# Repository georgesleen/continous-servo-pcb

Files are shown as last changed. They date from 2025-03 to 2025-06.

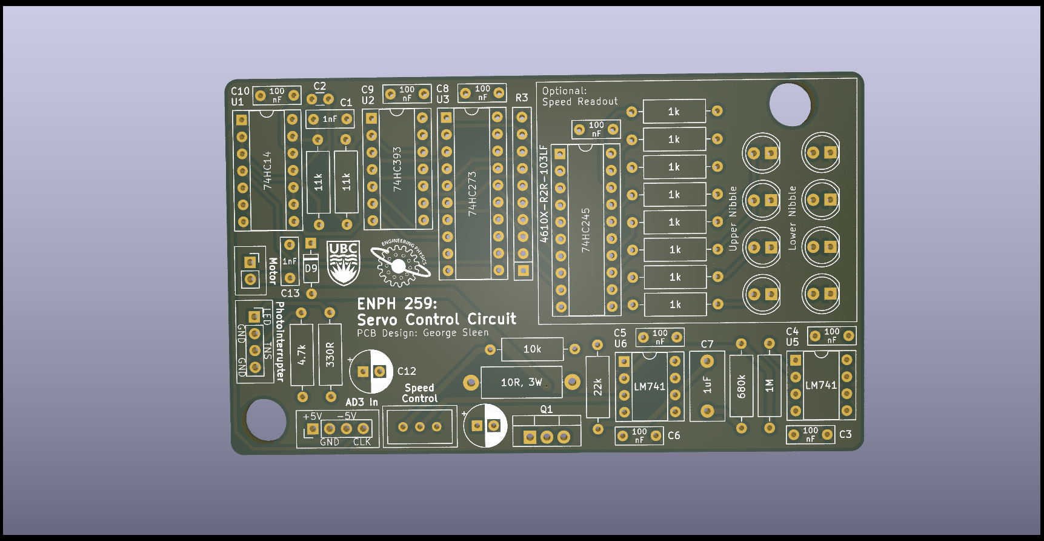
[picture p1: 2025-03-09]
images/enph259-servo-board-only.png

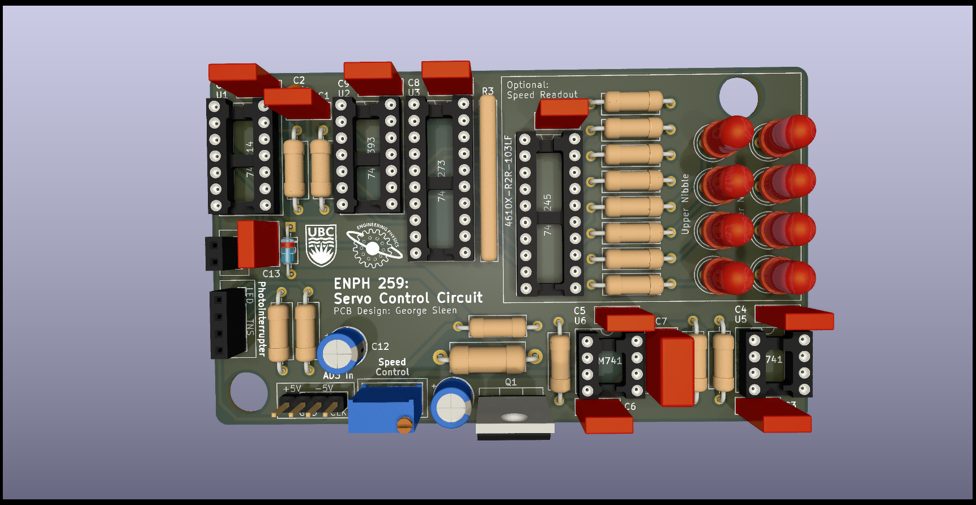
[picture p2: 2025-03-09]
images/enph259-servo.png

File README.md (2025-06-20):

# Continous rotation servo PCB.

Based on the final project from ENPH259. I've extended the project by creating a PCB and mechanical mount for the project.

I've also included an optional 'speed readout' on the board itself. This displays the current revolutions per cycle of the servo in binary.

By using slots in a disk attached to the motor shaft, I can monitor the rotational speed of the motor. This can then be fed into a counter that resets periodically, and is latched right before every reset. This digital number is then put through an R2R DAC, which is then compared with a reference voltage and fed into a PI controller, that runs a MOSFET driving the motor.

The project requires an external 5V, GND, -5V, and 5 Hz clock signal.

final-product
enph259-servo
enph259-servo-board-only

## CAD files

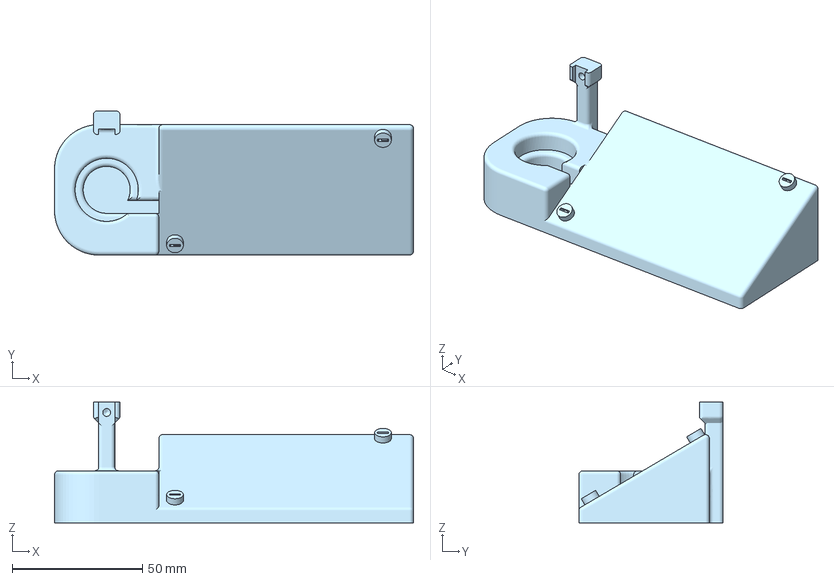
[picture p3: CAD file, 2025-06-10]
mount/enph259-pcb-mount.3mf
137.6 x 55.2 x 46.4 mm

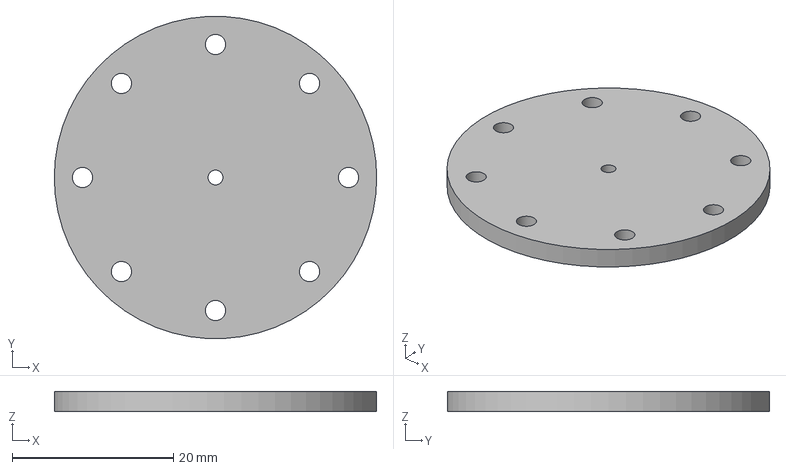
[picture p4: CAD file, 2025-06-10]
mount/enph259-photointerrupter-disk.3mf
40.0 x 39.9 x 2.50 mm

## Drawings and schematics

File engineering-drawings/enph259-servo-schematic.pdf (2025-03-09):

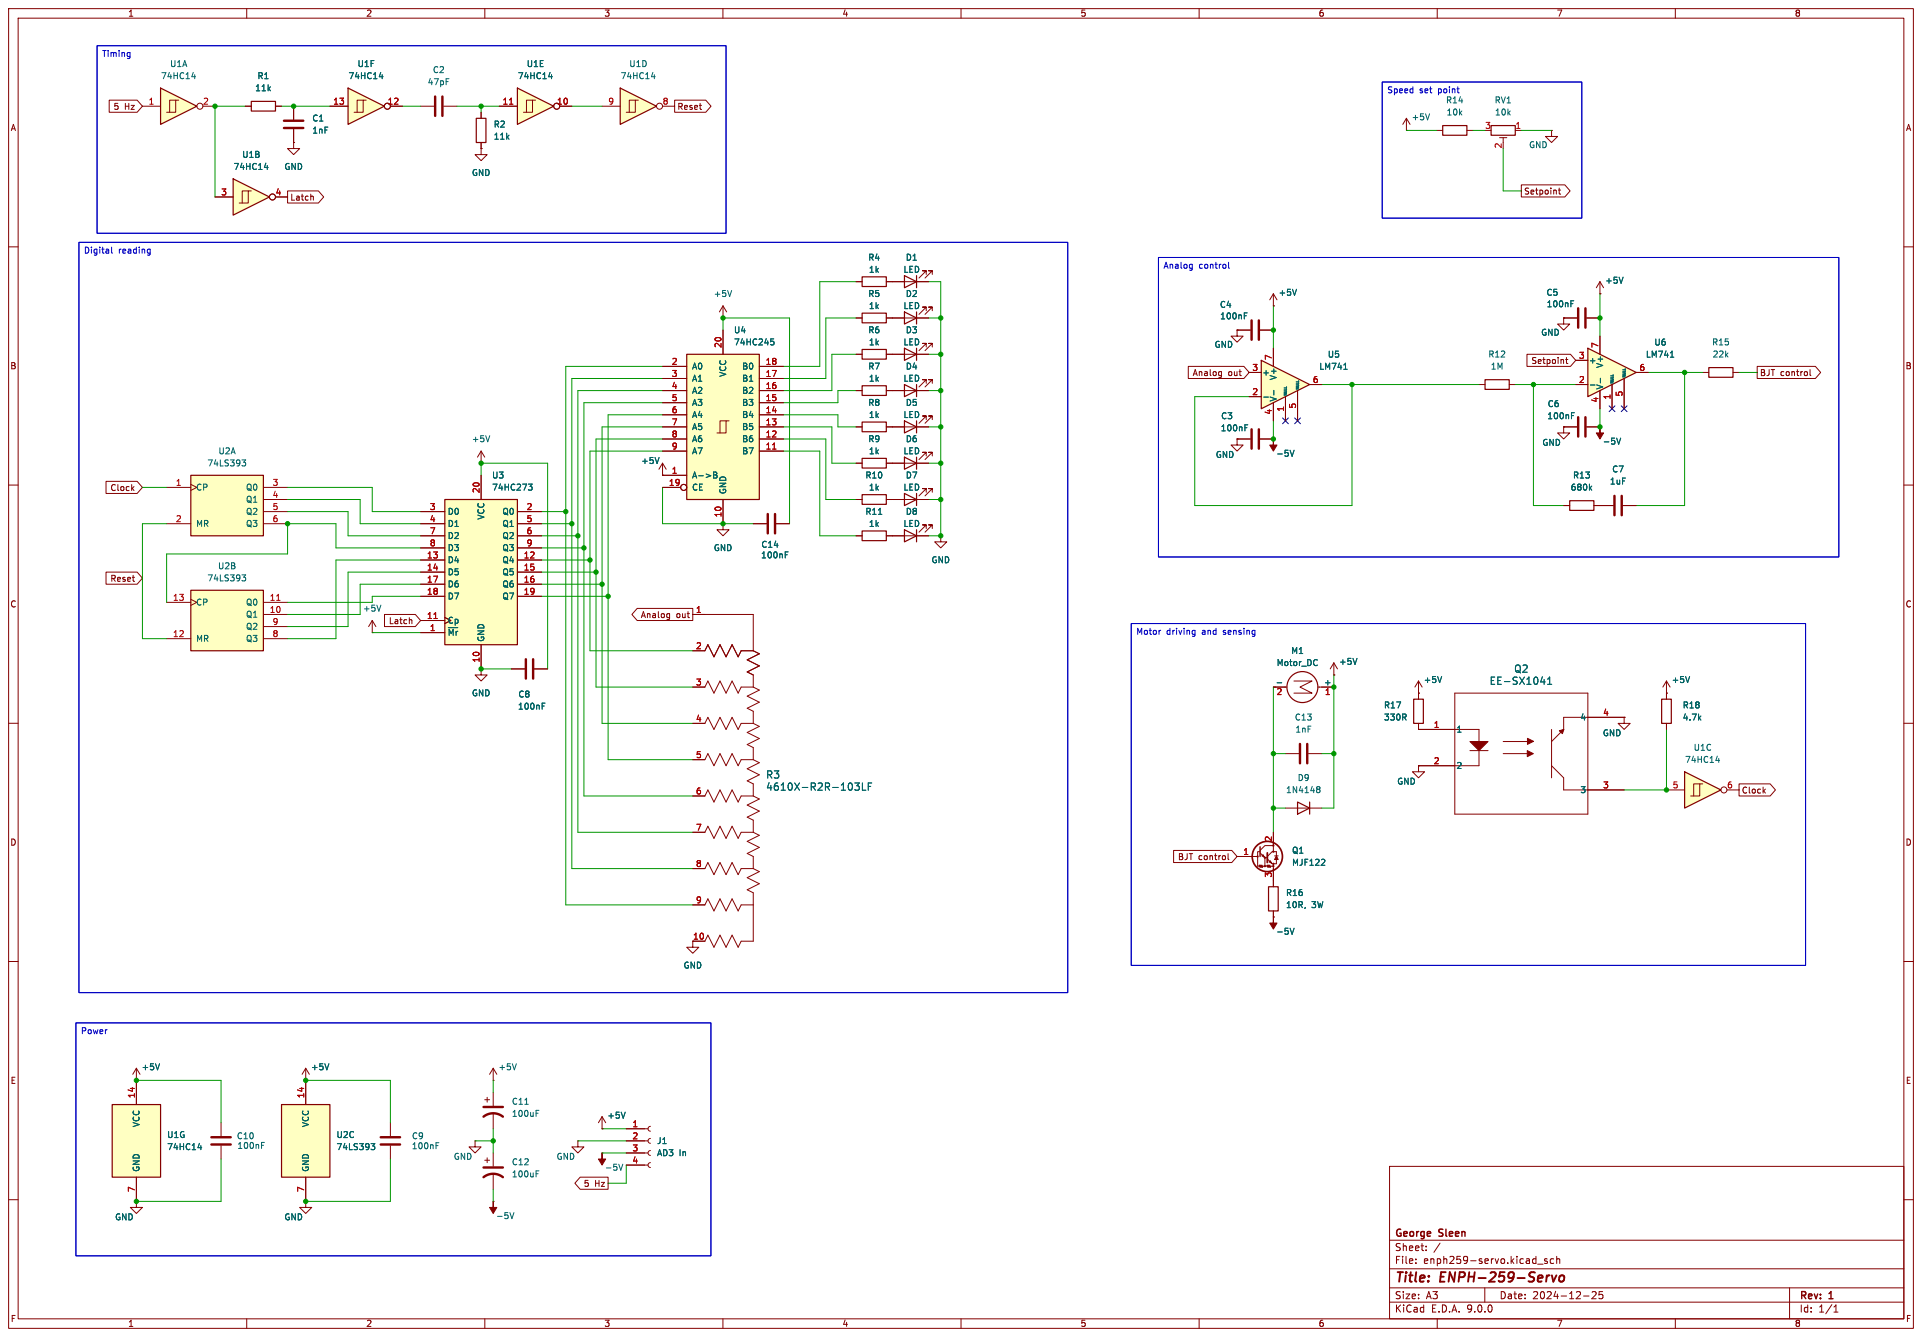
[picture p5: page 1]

Speed set point D7
Analog control Motor driving and sensing

File: enph259-servo.kicad_sch Sheet: / George Sleen

Id: 1/1 Title: ENPH-259-Servo

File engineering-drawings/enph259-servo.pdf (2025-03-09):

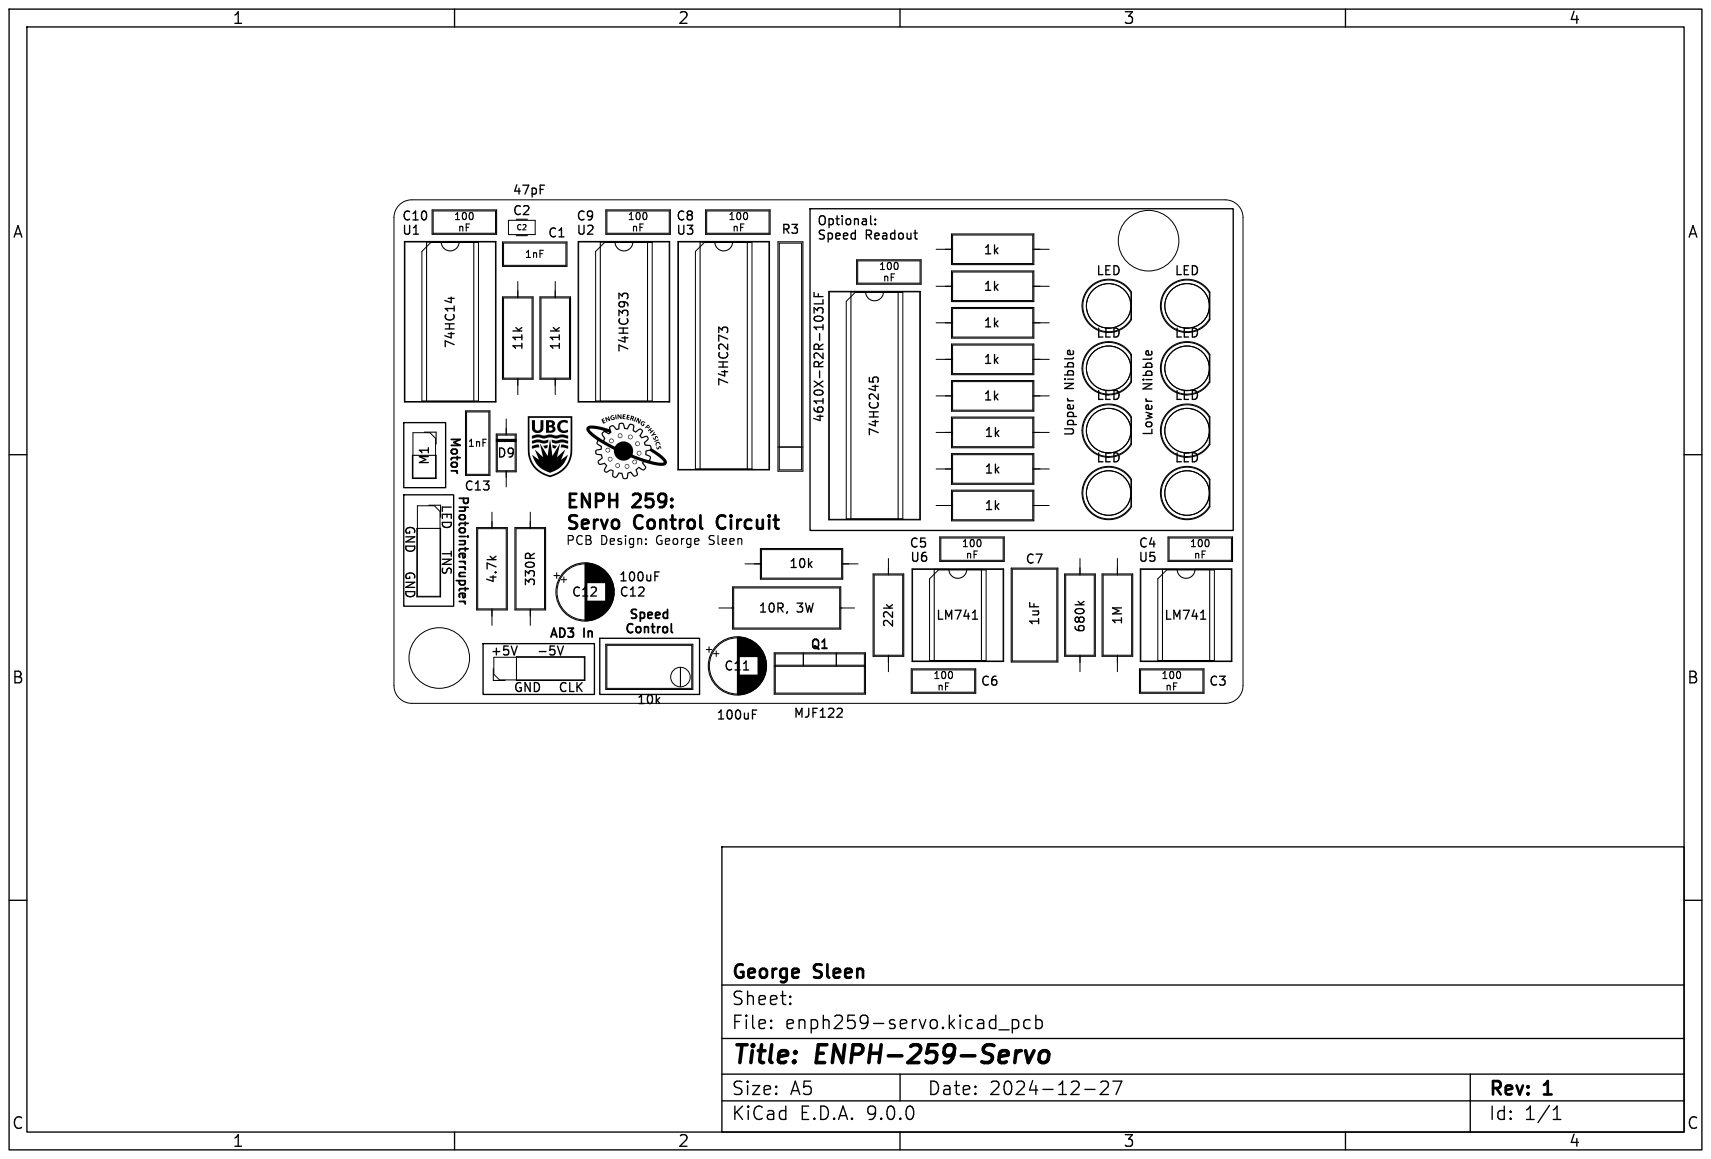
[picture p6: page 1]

File: enph259-servo.kicad_pcb Sheet: George Sleen 74HC245 Speed Control TNS Motor GND

Id: 1/1 Title: ENPH-259-Servo

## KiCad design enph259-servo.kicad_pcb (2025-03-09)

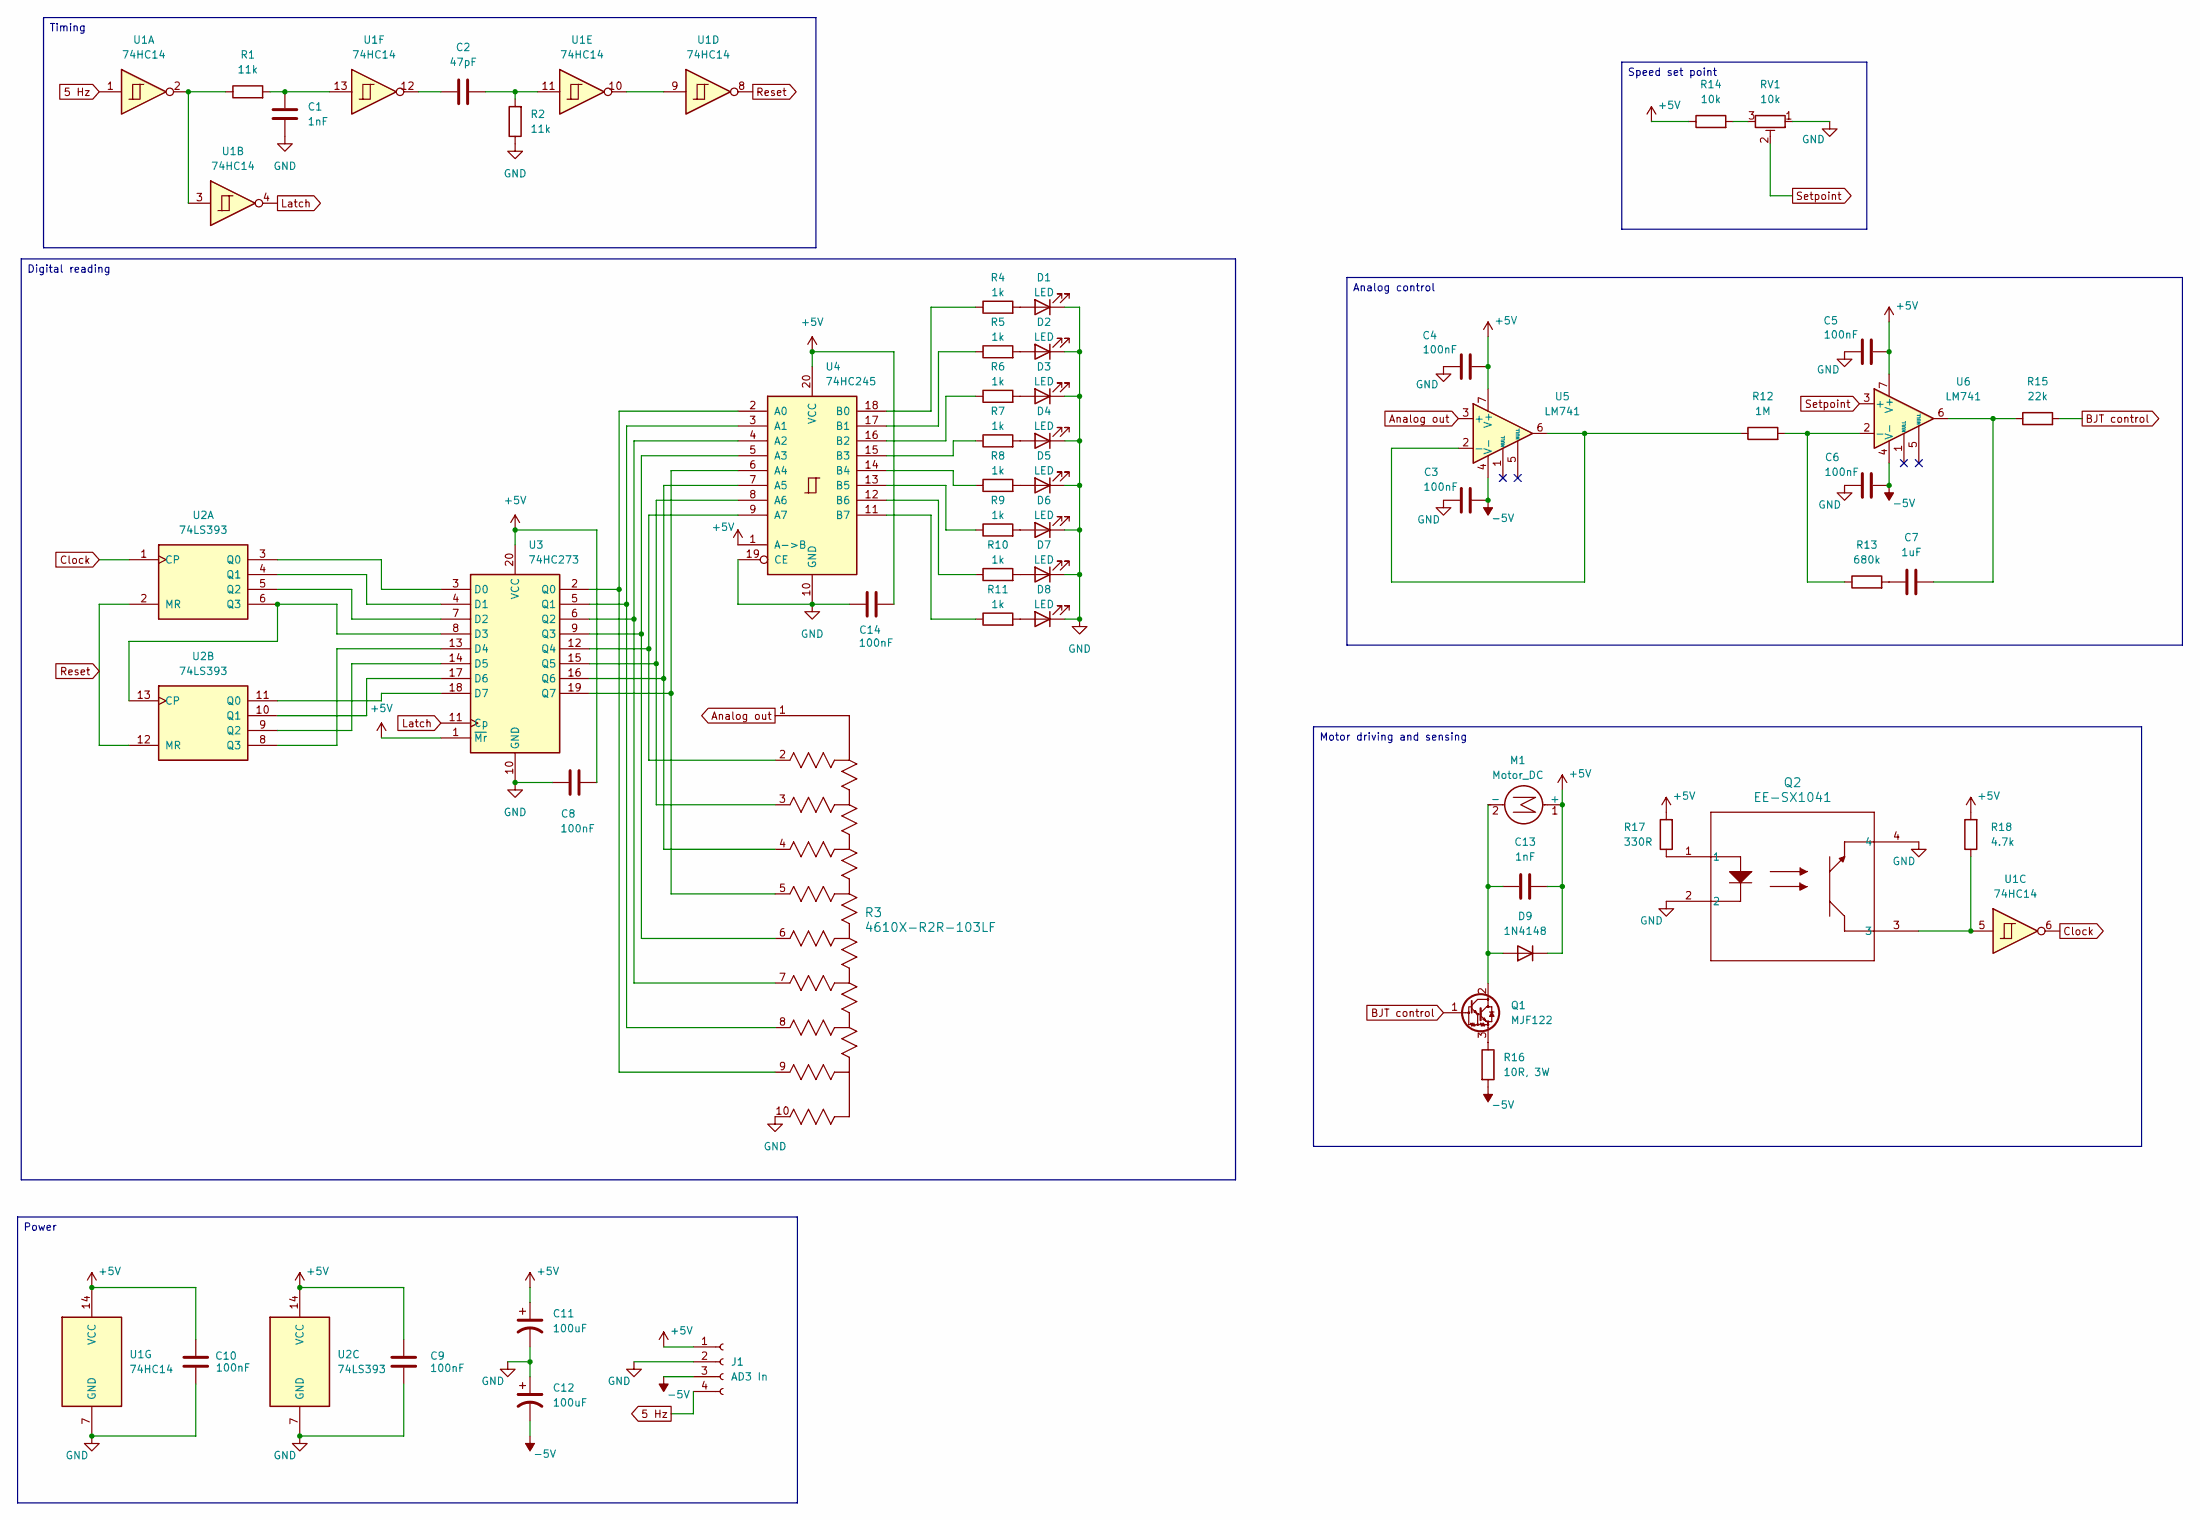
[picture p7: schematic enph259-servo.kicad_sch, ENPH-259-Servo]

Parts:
C1, C13: 1nF; C_Rect_L7.0mm_W2.5mm_P5.00mm
C2: 47pF; C_Disc_D3.0mm_W1.6mm_P2.50mm
C3, C4, C5, C6, C8, C9, C10, C14: 100nF; C_Rect_L7.0mm_W2.5mm_P5.00mm
C7: 1uF; C_Rect_L10.3mm_W5.0mm_P7.50mm_MKS4
C11, C12: 100uF; CP_Radial_D6.3mm_P2.50mm
D1, D2, D3, D4, D5, D6, D7, D8: LED; LED_D5.0mm
D9: 1N4148; D_DO-35_SOD27_P7.62mm_Horizontal
J1: AD3 In; PinHeader_1x04_P2.54mm_Vertical
M1: Motor_DC; PinSocket_1x02_P2.54mm_Vertical
Q1: MJF122; TO-220-3_Vertical
Q2: EE-SX1041; PinSocket_1x04_P2.54mm_Vertical
R1, R2: 11k; R_Axial_DIN0309_L9.0mm_D3.2mm_P12.70mm_Horizontal
R3: 4610X-R2R-103LF; R_Array_SIP10
R4, R5, R6, R7, R8, R9, R10, R11: 1k; R_Axial_DIN0309_L9.0mm_D3.2mm_P12.70mm_Horizontal
R12: 1M; R_Axial_DIN0309_L9.0mm_D3.2mm_P12.70mm_Horizontal
R13: 680k; R_Axial_DIN0309_L9.0mm_D3.2mm_P12.70mm_Horizontal
R14: 10k; R_Axial_DIN0309_L9.0mm_D3.2mm_P12.70mm_Horizontal
R15: 22k; R_Axial_DIN0309_L9.0mm_D3.2mm_P12.70mm_Horizontal
R16: 10R, 3W; R_Axial_DIN0414_L11.9mm_D4.5mm_P15.24mm_Horizontal
R17: 330R; R_Axial_DIN0309_L9.0mm_D3.2mm_P12.70mm_Horizontal
R18: 4.7k; R_Axial_DIN0309_L9.0mm_D3.2mm_P12.70mm_Horizontal
RV1: 10k; Potentiometer_Bourns_3296W_Vertical
U1: 74HC14; DIP-14_W7.62mm_Socket
U2: 74LS393; DIP-14_W7.62mm_Socket
U3: 74HC273; DIP-20_W7.62mm_Socket
U4: 74HC245; DIP-20_W7.62mm_Socket
U5, U6: LM741; DIP-8_W7.62mm_Socket

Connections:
5 Hz: J1.4, U1.1
+5V: C4.1, C5.1, C8.1, C9.1, C10.1, C11.1, C13.2, C14.2, D9.1 (K), J1.1, M1.1 (+), R14.1, R17.2, R18.2, U1.14 (VCC), U2.14 (VCC), U3.1 (~Mr), U3.20 (VCC), U4.1 (A->B), U4.20 (VCC), U5.7 (V+), U6.7 (V+)
-5V: C3.1, C6.1, C12.2, J1.3, R16.2, U5.4 (V-), U6.4 (V-)
Analog out: R3.1, U5.3 (+)
BJT control: Q1.1 (B), R15.2
Clock: U1.6, U2.1 (CP)
GND: C1.2, C3.2, C4.2, C5.2, C6.2, C8.2, C9.2, C10.2, C11.2, C12.1, C14.1, D1.1 (K), D2.1 (K), D3.1 (K), D4.1 (K), D5.1 (K), D6.1 (K), D7.1 (K), D8.1 (K), J1.2, Q2.2, Q2.4, R2.1, R3.10, RV1.1, U1.7 (GND), U2.7 (GND), U3.10 (GND), U4.10 (GND), U4.19 (CE)
Latch: U1.4, U3.11 (Cp)
unnamed: C1.1, R1.2, U1.13
unnamed: C2.1, U1.12
unnamed: C2.2, R2.2, U1.11
unnamed: C7.1, R13.2
unnamed: C7.2, R15.1, U6.6
unnamed: D1.2 (A), R4.2
unnamed: D2.2 (A), R5.2
unnamed: D3.2 (A), R6.2
unnamed: D4.2 (A), R7.2
unnamed: D5.2 (A), R8.2
unnamed: D6.2 (A), R9.2
unnamed: D7.2 (A), R10.2
unnamed: D8.2 (A), R11.2
unnamed: C13.1, D9.2 (A), M1.2 (-), Q1.2 (C)
unnamed: Q1.3 (E), R16.1
unnamed: Q2.1, R17.1
unnamed: Q2.3, R18.1, U1.5
unnamed: R1.1, U1.2, U1.3
unnamed: R14.2, RV1.3
unnamed: U1.9, U1.10
unnamed: U2.3 (Q0), U3.3 (D0)
unnamed: U2.4 (Q1), U3.4 (D1)
unnamed: U2.5 (Q2), U3.7 (D2)
unnamed: U2.6 (Q3), U2.13 (CP), U3.8 (D3)
unnamed: U2.11 (Q0), U3.18 (D7)
unnamed: U2.10 (Q1), U3.17 (D6)
unnamed: U2.9 (Q2), U3.14 (D5)
unnamed: U2.8 (Q3), U3.13 (D4)
unnamed: R3.9, U3.2 (Q0), U4.2 (A0)
unnamed: R3.8, U3.5 (Q1), U4.3 (A1)
unnamed: R3.7, U3.6 (Q2), U4.4 (A2)
unnamed: R3.6, U3.9 (Q3), U4.5 (A3)
unnamed: R3.2, U3.12 (Q4), U4.9 (A7)
unnamed: R3.3, U3.15 (Q5), U4.8 (A6)
unnamed: R3.4, U3.16 (Q6), U4.7 (A5)
unnamed: R3.5, U3.19 (Q7), U4.6 (A4)
unnamed: R4.1, U4.18 (B0)
unnamed: R5.1, U4.17 (B1)
unnamed: R6.1, U4.16 (B2)
unnamed: R7.1, U4.15 (B3)
unnamed: R8.1, U4.14 (B4)
unnamed: R9.1, U4.13 (B5)
unnamed: R10.1, U4.12 (B6)
unnamed: R11.1, U4.11 (B7)
unnamed: R12.1, U5.2 (-), U5.6
unnamed: R12.2, R13.1, U6.2 (-)
Reset: U1.8, U2.2 (MR), U2.12 (MR)
Setpoint: RV1.2, U6.3 (+)

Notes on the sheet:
Digital reading
Motor driving and sensing
Power
Speed set point
Analog control
Timing

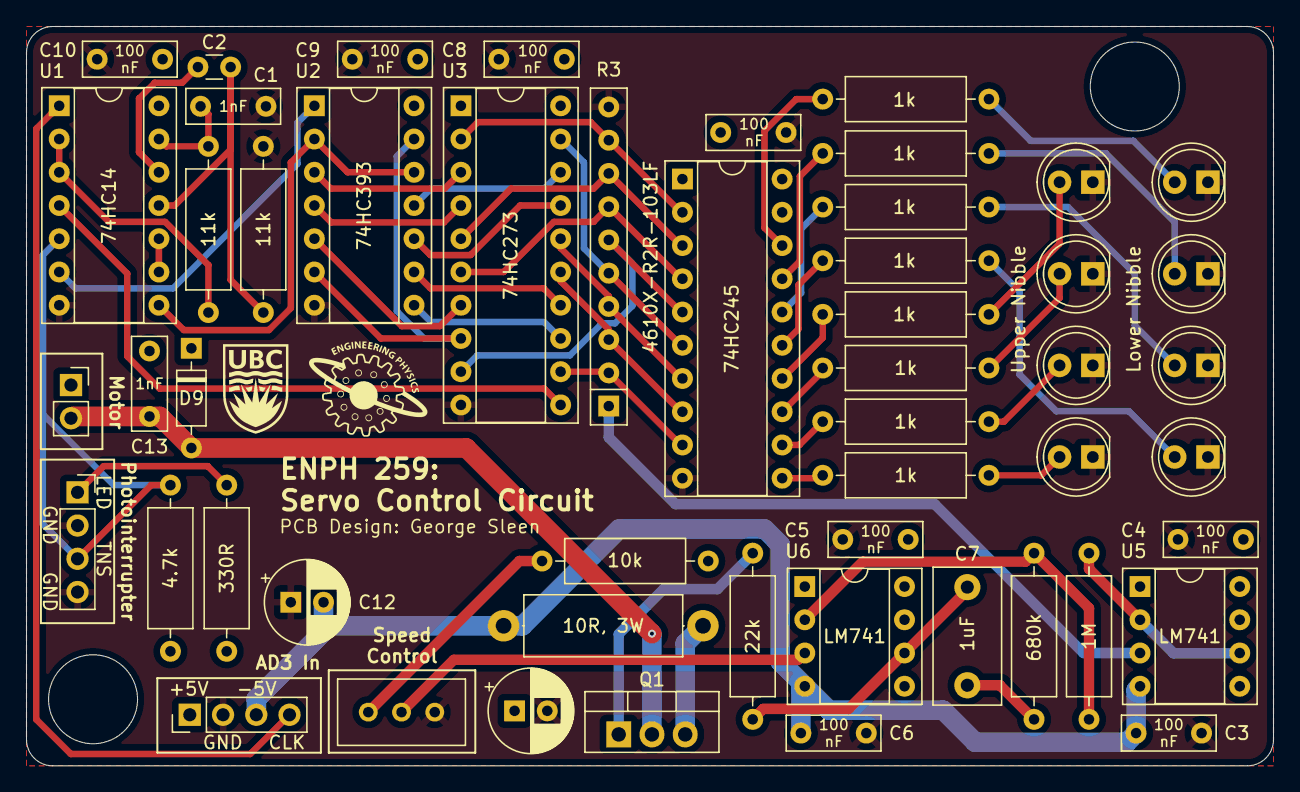
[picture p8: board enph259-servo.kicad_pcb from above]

Board: 4 copper layers, 95.3 x 56.5 mm, 52 parts (0 on the bottom side), 56 nets.

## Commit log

2025-03-09 Import existing project
    [enph259-servo-B_Cu.gbr, enph259-servo-B_Mask.gbr, enph259-servo-B_Paste.gbr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]
2025-06-10 Add some mount mechanical cad
    [enph259-pcb-mount.3mf, enph259-photointerrupter-disk.3mf]
2025-06-10 standardize capitalization
    [enph259-pcb-mount.3mf, enph259-photointerrupter-disk.3mf]
